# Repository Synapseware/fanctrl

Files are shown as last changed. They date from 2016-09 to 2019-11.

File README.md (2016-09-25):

Fan Controller
==============

Computer case fan speed controller, which uses a simple "fixed" buck converter for controller fan voltage.

PWM is not ideal for DC brushless fans, especially if you want to get constant data from the speed sensor.  This circuit forms a very simple buck converter by using a high-switching frequency coupled with the standard inductor, capacitor and diode.

# ADC Input
The ADC is configured for free-running mode.  The input to the ADC should pass through an RC filter or an RLC filter for improved noise immunity.

## Input Pin
The ADC is configured to read from PB4.

## ADC Sense Line
The input to the ADC should be constrained to 0.0v through 1.1v.  This gives the most accuracy on the ADC and allows for a small load/sense resistor.

# PWM Output
Timer1 is used in a Fast-PWM configuration with the 64mHz PLL clock.  This allows for a maximum of 250kHz switching frequency.  Relatively low by today's standards but very workable on a proto board or hand-made board.

## PWM Output Pin
The PWM output is available on PB1.  The output should not be filtered since it must be fed to the SMPS switching element.  Care should be taken to keep this line short and include an appropriately sized pull-down/pull-up resistor to ensure safe operation of the power MOSFET or other switching transistor.

# Other Chip Information
The AVR uC is configured to use it's internal R/C oscillator.  High clock accuracy is not needed by this circuit and keeping the part count low is a goal of this example.

# Build
This project compiles and uploads just fine using Linux and avr-gnu.

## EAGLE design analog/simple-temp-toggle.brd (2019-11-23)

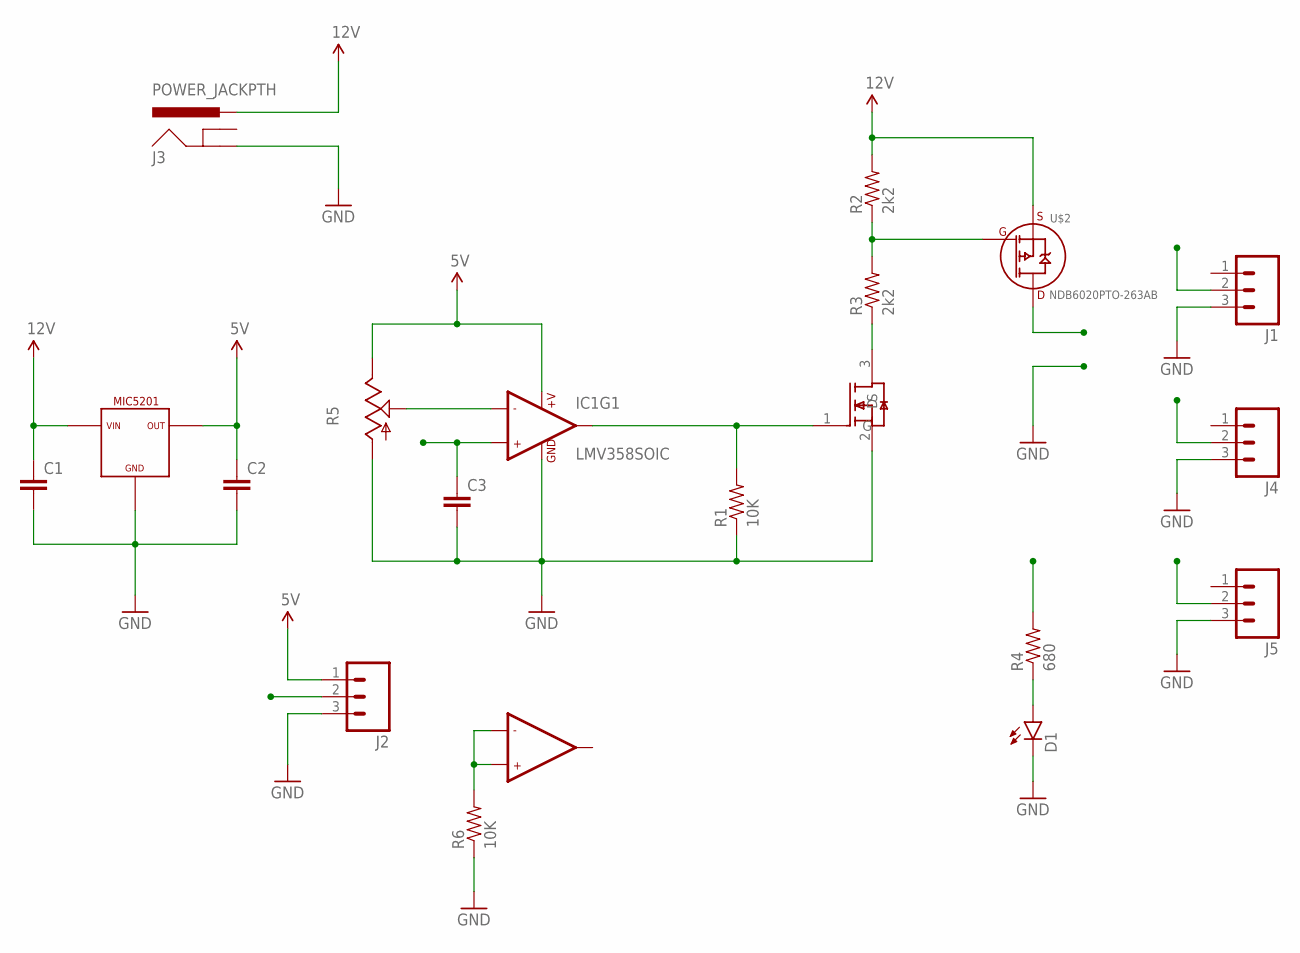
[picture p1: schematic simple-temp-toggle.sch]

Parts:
C1, C2, C3: 2.2UF50V10%(1206); 1206-CAP
D1: LED-FKIT-1206; FKIT-LED-1206
IC1: LMV358SOIC; SO08
J1, J2, J4, J5: M03LONGPADS; 1X03_LONGPADS
J3: POWER_JACKPTH; POWER_JACK_PTH
R1, R6: 10K; 1206
R2, R3: 2k2; 1206
R4: 680; 1206
R5: TRIM_US-S64W; S64W
U$2: NDB6020PTO-263AB; TO-263AB
U$3: MIC5201SOT-223; SOT-223
U$4: DMG2302UKSOT-23-3; SOT-23-3

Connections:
5V: C2.1, IC1.8 (+V), J2.1, R5.E, U$3.3 (OUT)
12V: C1.1, J3.PWR, R2.2, U$2.3 (S), U$3.1 (IN)
FAN_CTRL: IC1.1 (OUT1), R1.2, U$4.1 (G)
FAN_PWR: J1.2, J4.2, J5.2, R4.2, U$2.4 (D)
GND: C1.2, C2.2, C3.2, D1.C, IC1.4 (GND), J1.3, J2.3, J3.GND, J4.3, J5.3, R1.1, R5.A, R6.1, U$3.2 (GND), U$4.2 (S)
unnamed: IC1.2 (-IN1), R5.S
unnamed: IC1.5 (+IN2), IC1.6 (-IN2), R6.2
unnamed: D1.A, R4.1
unnamed: R2.1, R3.2, U$2.1 (G)
unnamed: R3.1, U$4.3 (D)
TMP_SENSOR: C3.1, IC1.3 (+IN1), J2.2

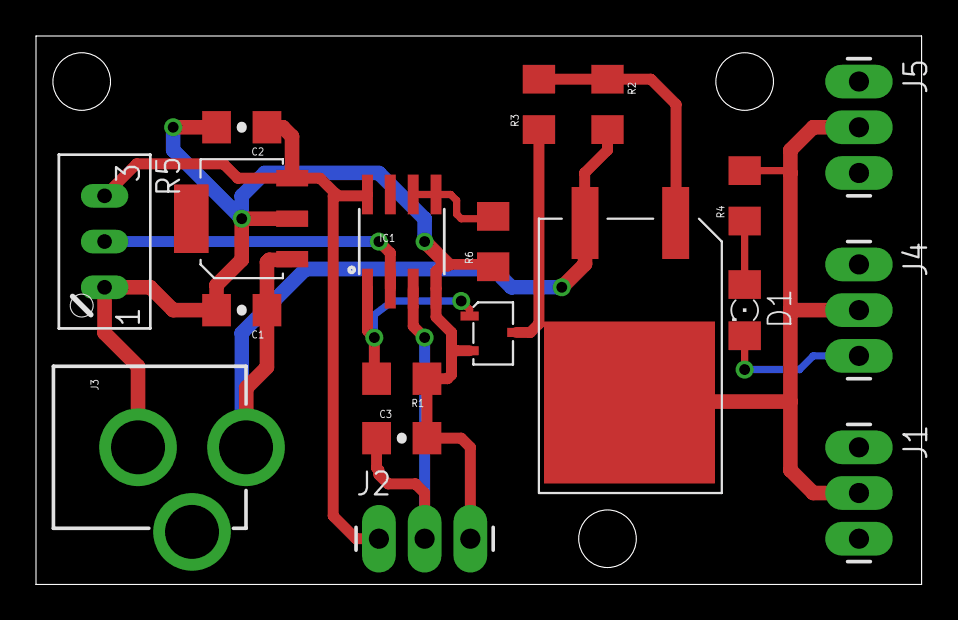
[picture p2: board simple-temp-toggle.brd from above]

Board: 2 copper layers, 49.2 x 30.5 mm, 19 parts (0 on the bottom side), 11 nets.

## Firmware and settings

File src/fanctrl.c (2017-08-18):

#include "fanctrl.h"

volatile uint8_t	tick		= 0;
volatile uint8_t 	adcData		= 0;



//----------------------------------------------------------------
// Gets the MUX configuration bits for the specified channel
static void ConfigureADC(uint8_t channel)
{
	channel &= 0x07;

	// get the MUX value 
	uint8_t mux =	(ADMUX & 0xF0) |	// mask out the channel bits
					(channel);			// set the channel

	// disable digital input on the selected channel
	DIDR0 = (1<<channel);

	// set the pin as input
	DDRC &= ~(1<<channel);

	// set the MUX register
	ADMUX = mux;
}


//----------------------------------------------------------------
// Setup ADC to read from the temp sensor.  External analog reference
// voltage is 2.5V
static void initADC(void)
{
	ConfigureADC(ADC_CHANNEL);

	ADMUX	|=	(0<<ADLAR);		// Right adjust result

	ADCSRA	=	(1<<ADEN)	|	// ADC Enable
				(0<<ADSC)	|	// 
				(0<<ADATE)	|	// 
				(0<<ADIF)	|	// 
				(1<<ADIE)	|	// Enable interrupts
				(1<<ADPS2)	|	// Prescaler of 64
				(1<<ADPS1)	|	// 8MHz / 64 = 125kHz ADC clock
				(0<<ADPS0);		// ...

	ADCSRB	=	(0<<ACME)	|	// Disable the analog comparator
				(0<<ADTS2)	|	// Free running mode
				(0<<ADTS1)	|	// ...
				(0<<ADTS0);		// ...
}


//----------------------------------------------------------------
// Setup timer1
static void initSystemTimer(void)
{
	// FCPU / 256 / 3125 = 10Hz
	// 8MHz / 256 / 3125 = 10

	TCCR1A	=	(0<<COM1A1)	|
				(0<<COM1A0)	|
				(0<<COM1B1)	|
				(0<<COM1B0)	|
				(0<<WGM11)	|	// CTC
				(0<<WGM10);		// CTC

	TCCR1B	=	(0<<ICNC1)	|
				(0<<ICES1)	|
				(0<<WGM13)	|	// CTC
				(1<<WGM12)	|	// CTC
				(1<<CS12)	|	// FCPU/256
				(0<<CS11)	|	// ...
				(0<<CS10);		// ...

	TIMSK1	=	(0<<ICIE1)	|
				(0<<OCIE1B)	|
				(1<<OCIE1A)	|	// Compare A interrupt enable
				(0<<TOIE1);

	OCR1A	=	3125-1;
	OCR1B	=	0xffff;
}


//----------------------------------------------------------------
// Setup the USI for SPI mode
static void initSPI(void)
{
	SPCR	=	(0<<SPIE)	|	// 
				(1<<SPE)	|	// Bit 6 – SPE: SPI Enable
				(0<<DORD)	|	// 
				(1<<MSTR)	|	// Master mode
				(0<<CPOL)	|	// 
				(0<<CPHA)	|	// 
				(1<<SPR1)	|	// Fosc = Fcpu / 64
				(0<<SPR0);		// ...

	SPSR	=	(0<<SPIF)	|	// 
				(0<<WCOL)	|	// 
				(0<<SPI2X);		// No double speed

	// configure the /CS pin for output
	SPI_PORT	|= (1<<SPI_CS) | (1<<SPI_DO) | (1<<SPI_CLK);
	SPI_DDR		|= (1<<SPI_CS) | (1<<SPI_DO) | (1<<SPI_CLK);
}


//----------------------------------------------------------------
// 
static void init(void)
{
    power_adc_enable();
    power_spi_enable();
    power_timer0_enable();
    power_timer1_enable();

	initSystemTimer();

	initADC();

	initSPI();

	sei();
}


//----------------------------------------------------------------
// Converts the value from the temperature sensor to degrees C
static int ConvertToCelcius(int temp)
{
	// Temperature sensor is a TMP35

	// ADC is configured to read the 8 most significant bits only
	// ADC value = (Vin * 1024) / Vref
	//			Vin * 1024
	// result = ----------
	//			   5.0v
	//

	return temp;
}


//----------------------------------------------------------------
// Writes a byte of data to the SPI bus
static uint8_t writeByte(uint8_t data)
{
	// write to the data register
	SPDR = data;

	// wait for data to be transfered
	while(!(SPSR & (1<<SPIF)))
		;

	return SPDR;
}


//----------------------------------------------------------------
// Configures the digital resistor to the given value
static void setResistorValue(int value)
{
	SPI_PORT &= ~(1<<SPI_CS);

	// we only need the top 7 bits
	value >>= 3;

	writeByte(MCP_WRITE_WP0);
	writeByte(value & 0x7F);

	SPI_PORT |= (1<<SPI_CS);
}


//----------------------------------------------------------------
// 
static uint8_t GetLatestAdcData(void)
{
	return adcData;
}


//----------------------------------------------------------------
// Smooths the ADC value by averaging readings
static void SmoothADCValue(int value)
{
	adcData = (value>>2) + adcData - (adcData>>2);
}


//----------------------------------------------------------------
// 
int main(void)
{
	init();

	// start the first conversion
	ADCSRA |= (1<<ADSC);

	DDRB |= (1<<LED_DBG);
	PORTB &= ~(1<<LED_DBG);

	while(1)
	{
		if (!tick)
			continue;

		// toggle the debug LED
		//PINB |= (1<<LED_DBG);
		PORTB |= (1<<LED_DBG);

		// convert the ADC data to Celcius
		uint8_t temp = ConvertToCelcius(GetLatestAdcData());

		// update the resistor ladder with new data
		setResistorValue(temp);

		// reset the tick
		tick = 0;
		PORTB &= ~(1<<LED_DBG);
	}

	return 0;
}


//----------------------------------------------------------------
// ADC interrupt complete handler
ISR(ADC_vect)
{
	// just read the ADCH register (top 8 bits)
	SmoothADCValue(ADC);
}


//----------------------------------------------------------------
// Timer 1 compare A interrupt handler
ISR(TIMER1_COMPA_vect)
{
	static uint8_t delay = DELAY;

	if (delay--)
		return;

	delay = DELAY;

	tick = 1;

	// start another ADC conversion
	ADCSRA |= (1<<ADSC);
}

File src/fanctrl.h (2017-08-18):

#ifndef __FANCTRL_H__
#define __FANCTRL_H__


#include <avr/io.h>
#include <avr/interrupt.h>
#include <inttypes.h>
#include <avr/sleep.h>
#include <avr/power.h>
#include <util/delay.h>


//--------------------------------------------------
// Board constants
#define	ADC_CHANNEL		0
#define ADC_SMOOTHING	4
#define DELAY			10


#define LED_DBG			PB0

#define SPI_CLK			PB5
#define SPI_DI			PB4
#define SPI_DO			PB3
#define SPI_CS			PB2
#define SPI_DDR			DDRB
#define SPI_PORT		PORTB


//--------------------------------------------------
// MCP41x1 driver data
#define MCP_A3			7
#define MCP_A2			6
#define MCP_A1			5
#define MCP_A0			4
#define MCP_C1			3
#define MCP_C0			2
#define MCP_D1			1
#define MCP_D0			0

#define MCP_WIPER_0		0x00
#define MCP_WIPER_1		0x01
#define MCP_TCON_REG	0x04
#define MCP_STATUS_REG	0x05

#define MCP_WRITE_WP0	0x00
#define MCP_READ_WP0	0x0C
#define MCP_INC_WP0		0x04
#define MCP_DEC_WP0		0x08

#define MCP_WRITE_WP1	0x10
#define MCP_READ_WP1	0x1C
#define MCP_INC_WP1		0x14
#define MCP_DEC_WP1		0x18


#endif

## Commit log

2016-09-25 Working on PWM frequency & config
2016-09-27 Updates for the fan controller
2017-02-12 Updating the fancontroller
    [fancontroller.sch]
2017-02-12 Initial draft of fan controller
    There's probably a MUCH easier way to do this, but it's fun.
2017-02-13 Converting to use ATMega168
    Too many problems with the Tiny85: timers, interrupts, SPI, etc.
    [fanctrl.c, fanctrl.h]
2017-02-13 ATMega168 version is mostly functional
    Transform function(s) not yet implemented, so there's no conversion from
    external temp sensor to control the fan speed.
2017-02-23 WIP: Not sending correct data to the digital resistor
    The circuit works, the ADC works, but it's not sending the correct data
    to the MCP4131-103 (a 10k digital potentiometer). Next up, is to write
    canned data.
    [fanctrl.c, fanctrl.h]
2018-01-05 Capturing protoboard layout
    [fancontroller.sch]
2019-09-16 Analog fan controller
    [analog-fan-controller.sch]
2019-11-23 Board updates
2019-11-23 New temp board
    [simple-temp-toggle.brd, simple-temp-toggle.sch]

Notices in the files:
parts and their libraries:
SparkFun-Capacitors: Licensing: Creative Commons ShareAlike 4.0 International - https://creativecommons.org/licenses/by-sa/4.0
